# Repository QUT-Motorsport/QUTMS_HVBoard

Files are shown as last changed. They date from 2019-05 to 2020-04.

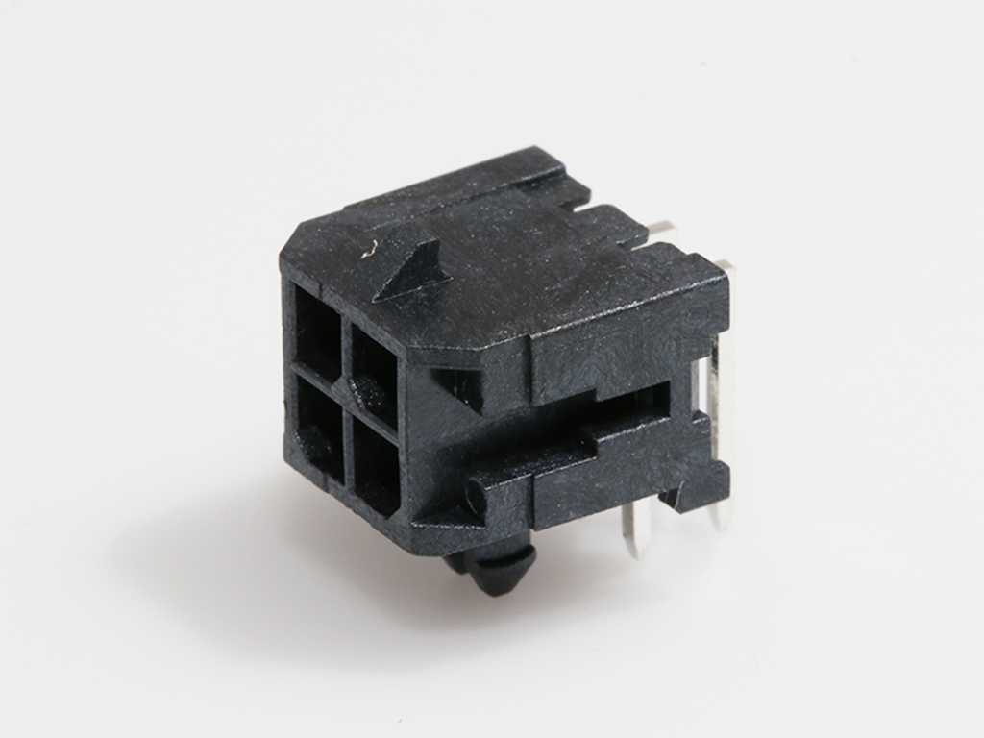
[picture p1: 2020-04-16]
hardware/QUTMS_HVBoard_V1_1/0430450400_hires.jpg

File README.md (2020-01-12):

QUTMS_Banner
# HV Board
The HV Board resides inside the HV box directly infront of the accumulator and monitors the tractive system in various ways.

## Features

- CANBUS Interface using the MCP2517 ic
- Isolated analog TSAL enable/disable signalling
- IMD state sensing and powering
- Tractive system current measurement
- UART debugging header

## Functions

Whilst the BSPD circitry is located on the shutdown board, the HV board powers the device and has an amplifier to boost the signal before it makes its way through the wiring harness.

In order to detect when the tractive system has a voltage more than 60V present, there is an isolated circuit on board that compares a divided TS voltage with a reference voltage. It also has a mosfet to drive the TS active and TS inactive signals to the TSAL board.

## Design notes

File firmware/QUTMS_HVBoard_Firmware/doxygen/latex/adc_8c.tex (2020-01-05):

\hypertarget{adc_8c}{}\doxysection{adc.\+c File Reference}
\label{adc_8c}\index{adc.c@{adc.c}}

Analogue to digital conversion.  

{\ttfamily \#include \char`\"{}adc.\+h\char`\"{}}\newline
{\ttfamily \#include $<$avr/interrupt.\+h$>$}\newline
{\ttfamily \#include $<$avr/io.\+h$>$}\newline
{\ttfamily \#include $<$avr/pgmspace.\+h$>$}\newline
{\ttfamily \#include $<$util/delay.\+h$>$}\newline
\doxysubsection*{Functions}
\begin{DoxyCompactItemize}
\item 
void \mbox{\hyperlink{adc_8c_a1e942fcd91f79d49e4ddb8d7e9d3ef95}{adc\+\_\+init}} ()
\item 
void \mbox{\hyperlink{adc_8c_af95038404db6216aa1860a35929b90ac}{adc\+\_\+set\+\_\+prescalar}} (uint8\+\_\+t prescalar)
\item 
uint16\+\_\+t \mbox{\hyperlink{adc_8c_a67d34c1378ba0871293df7b6a387de60}{adc\+\_\+read}} (uint8\+\_\+t adc\+\_\+channel)
\end{DoxyCompactItemize}

\doxysubsection{Detailed Description}
Analogue to digital conversion. 

\begin{DoxyAuthor}{Author}
Zoe Goodward 
\end{DoxyAuthor}

\doxysubsection{Function Documentation}
\mbox{\Hypertarget{adc_8c_a1e942fcd91f79d49e4ddb8d7e9d3ef95}\label{adc_8c_a1e942fcd91f79d49e4ddb8d7e9d3ef95}} 
\index{adc.c@{adc.c}!adc\_init@{adc\_init}}
\index{adc\_init@{adc\_init}!adc.c@{adc.c}}
\doxysubsubsection{\texorpdfstring{adc\_init()}{adc\_init()}}
{\footnotesize\ttfamily void adc\+\_\+init (\begin{DoxyParamCaption}{ }\end{DoxyParamCaption})}

Initializes the analogue to digital conversion by first selecting the voltage reference and then setting the A\+DC Enable bit, A\+D\+EN in A\+D\+C\+S\+RA. \begin{DoxyReturn}{Returns}
void 
\end{DoxyReturn}
\mbox{\Hypertarget{adc_8c_a67d34c1378ba0871293df7b6a387de60}\label{adc_8c_a67d34c1378ba0871293df7b6a387de60}} 
\index{adc.c@{adc.c}!adc\_read@{adc\_read}}
\index{adc\_read@{adc\_read}!adc.c@{adc.c}}
\doxysubsubsection{\texorpdfstring{adc\_read()}{adc\_read()}}
{\footnotesize\ttfamily uint16\+\_\+t adc\+\_\+read (\begin{DoxyParamCaption}\item[{uint8\+\_\+t}]{adc\+\_\+channel }\end{DoxyParamCaption})}

Reads an analogue input voltage and converts it to a 10-\/bit digital value through successive approximation. 
\begin{DoxyParams}{Parameters}
{\em adc\+\_\+channel} & Selected analogue input channel \\
\hline
\end{DoxyParams}
\begin{DoxyReturn}{Returns}
Pass the 10 bit A\+DC number to requesting function 
\end{DoxyReturn}
\mbox{\Hypertarget{adc_8c_af95038404db6216aa1860a35929b90ac}\label{adc_8c_af95038404db6216aa1860a35929b90ac}} 
\index{adc.c@{adc.c}!adc\_set\_prescalar@{adc\_set\_prescalar}}
\index{adc\_set\_prescalar@{adc\_set\_prescalar}!adc.c@{adc.c}}
\doxysubsubsection{\texorpdfstring{adc\_set\_prescalar()}{adc\_set\_prescalar()}}
{\footnotesize\ttfamily void adc\+\_\+set\+\_\+prescalar (\begin{DoxyParamCaption}\item[{uint8\+\_\+t}]{prescalar }\end{DoxyParamCaption})}

Sets the prescalar. \begin{DoxyReturn}{Returns}
void 
\end{DoxyReturn}

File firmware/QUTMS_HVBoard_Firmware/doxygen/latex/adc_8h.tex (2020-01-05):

\hypertarget{adc_8h}{}\doxysection{adc.\+h File Reference}
\label{adc_8h}\index{adc.h@{adc.h}}

Analogue to digital conversion.  

{\ttfamily \#include $<$avr/io.\+h$>$}\newline
{\ttfamily \#include $<$util/delay.\+h$>$}\newline
{\ttfamily \#include $<$avr/interrupt.\+h$>$}\newline
{\ttfamily \#include $<$avr/pgmspace.\+h$>$}\newline
\doxysubsection*{Macros}
\begin{DoxyCompactItemize}
\item 
\#define \mbox{\hyperlink{adc_8h_a97010ca07f7fab62f9fb4b4c404e6a90}{A\+D\+C\+\_\+\+P\+R\+E\+S\+C\+A\+L\+E\+\_\+\+M\+A\+SK}}~0b11111000
\end{DoxyCompactItemize}
\doxysubsection*{Functions}
\begin{DoxyCompactItemize}
\item 
void \mbox{\hyperlink{adc_8h_a1e942fcd91f79d49e4ddb8d7e9d3ef95}{adc\+\_\+init}} ()
\item 
uint16\+\_\+t \mbox{\hyperlink{adc_8h_a67d34c1378ba0871293df7b6a387de60}{adc\+\_\+read}} (uint8\+\_\+t adc\+\_\+channel)
\end{DoxyCompactItemize}

\doxysubsection{Detailed Description}
Analogue to digital conversion. 

\begin{DoxyAuthor}{Author}
Zoe Goodward 
\end{DoxyAuthor}

\doxysubsection{Macro Definition Documentation}
\mbox{\Hypertarget{adc_8h_a97010ca07f7fab62f9fb4b4c404e6a90}\label{adc_8h_a97010ca07f7fab62f9fb4b4c404e6a90}} 
\index{adc.h@{adc.h}!ADC\_PRESCALE\_MASK@{ADC\_PRESCALE\_MASK}}
\index{ADC\_PRESCALE\_MASK@{ADC\_PRESCALE\_MASK}!adc.h@{adc.h}}
\doxysubsubsection{\texorpdfstring{ADC\_PRESCALE\_MASK}{ADC\_PRESCALE\_MASK}}
{\footnotesize\ttfamily \#define A\+D\+C\+\_\+\+P\+R\+E\+S\+C\+A\+L\+E\+\_\+\+M\+A\+SK~0b11111000}

\doxysubsection{Function Documentation}
\mbox{\Hypertarget{adc_8h_a1e942fcd91f79d49e4ddb8d7e9d3ef95}\label{adc_8h_a1e942fcd91f79d49e4ddb8d7e9d3ef95}} 
\index{adc.h@{adc.h}!adc\_init@{adc\_init}}
\index{adc\_init@{adc\_init}!adc.h@{adc.h}}
\doxysubsubsection{\texorpdfstring{adc\_init()}{adc\_init()}}
{\footnotesize\ttfamily void adc\+\_\+init (\begin{DoxyParamCaption}{ }\end{DoxyParamCaption})}

Initializes the analogue to digital conversion by first selecting the voltage reference and then setting the A\+DC Enable bit, A\+D\+EN in A\+D\+C\+S\+RA. \begin{DoxyReturn}{Returns}
void 
\end{DoxyReturn}
\mbox{\Hypertarget{adc_8h_a67d34c1378ba0871293df7b6a387de60}\label{adc_8h_a67d34c1378ba0871293df7b6a387de60}} 
\index{adc.h@{adc.h}!adc\_read@{adc\_read}}
\index{adc\_read@{adc\_read}!adc.h@{adc.h}}
\doxysubsubsection{\texorpdfstring{adc\_read()}{adc\_read()}}
{\footnotesize\ttfamily uint16\+\_\+t adc\+\_\+read (\begin{DoxyParamCaption}\item[{uint8\+\_\+t}]{adc\+\_\+channel }\end{DoxyParamCaption})}

Reads an analogue input voltage and converts it to a 10-\/bit digital value through successive approximation. 
\begin{DoxyParams}{Parameters}
{\em adc\+\_\+channel} & Selected analogue input channel \\
\hline
\end{DoxyParams}
\begin{DoxyReturn}{Returns}
Pass the 10 bit A\+DC number to requesting function 
\end{DoxyReturn}

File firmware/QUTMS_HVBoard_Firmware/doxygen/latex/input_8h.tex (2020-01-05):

\hypertarget{input_8h}{}\doxysection{input.\+h File Reference}
\label{input_8h}\index{input.h@{input.h}}

This file defines the outputs and inputs of the pins of the M\+CU test.  

\doxysubsection*{Macros}
\begin{DoxyCompactItemize}
\item 
\#define \mbox{\hyperlink{input_8h_ad344f4bc1bb96945391f1edcd2060d60}{C\+A\+N\+\_\+\+C\+S\+\_\+\+P\+O\+RT}}~P\+O\+R\+TB
\item 
\#define \mbox{\hyperlink{input_8h_ab8cc8ec9bfd0e83fbc693b57f91545b1}{C\+A\+N\+\_\+\+CS}}~P\+I\+N\+B3
\item 
\#define \mbox{\hyperlink{input_8h_a5e4af61c9cda09a07019a625496aad51}{C\+A\+N\+\_\+\+I\+NT}}~P\+I\+N\+B0
\item 
\#define \mbox{\hyperlink{input_8h_ab7f73ee6874d571893c07b78293b9524}{L\+E\+D\+\_\+A}}~P\+I\+N\+D6
\item 
\#define \mbox{\hyperlink{input_8h_a2d0969469518b59d85bfa78504cffef9}{L\+E\+D\+\_\+B}}~P\+I\+N\+D7
\item 
\#define \mbox{\hyperlink{input_8h_a9fbaade4f52377099fe27dfde7cc6b34}{L\+E\+D\+\_\+\+A\+\_\+\+ON}}~P\+O\+R\+TD $\vert$= 0b01000000
\item 
\#define \mbox{\hyperlink{input_8h_ab351a7c43c4d7fe53191df69a0d0d4cb}{L\+E\+D\+\_\+\+A\+\_\+\+O\+FF}}~P\+O\+R\+TD \&= $\sim$0b01000000
\item 
\#define \mbox{\hyperlink{input_8h_a1429fd4e85c4d8e419b4a05aba730df5}{L\+E\+D\+\_\+\+B\+\_\+\+ON}}~P\+O\+R\+TD $\vert$= 0b10000000
\item 
\#define \mbox{\hyperlink{input_8h_a1552ab4bdb99c586585fc78c969848bc}{L\+E\+D\+\_\+\+B\+\_\+\+O\+FF}}~P\+O\+R\+TD \&= $\sim$0b10000000
\item 
\#define \mbox{\hyperlink{input_8h_af309cf9cb33c25c407e3b8679cf9d601}{L\+E\+D\+\_\+\+A\+\_\+\+T\+O\+G\+G\+LE}}~P\+O\+R\+TD $^\wedge$= 0b01000000
\item 
\#define \mbox{\hyperlink{input_8h_a0c1fba754d8d18f94fa73189b6fdcd78}{I\+M\+D\+\_\+\+R\+EG}}~P\+I\+NA
\item 
\#define \mbox{\hyperlink{input_8h_ac7e14c87447fabc3ab90eff695976def}{I\+M\+D\+\_\+\+S\+T\+A\+T\+US}}~P\+I\+N\+A2
\item 
\#define \mbox{\hyperlink{input_8h_a40c6fc36b705933b5671a86806cbdb3e}{H\+V\+\_\+\+S\+E\+N\+S\+E\+\_\+\+R\+EG}}~P\+I\+NA
\item 
\#define \mbox{\hyperlink{input_8h_a1ee6fbbcd4ac34f1c64c7e2d414127b1}{H\+V\+\_\+\+S\+E\+N\+S\+E\+\_\+\+S\+T\+A\+T\+US}}~P\+I\+N\+A0
\end{DoxyCompactItemize}

\doxysubsection{Detailed Description}
This file defines the outputs and inputs of the pins of the M\+CU test. 

\begin{DoxyAuthor}{Author}
Zoe Goodward 
\end{DoxyAuthor}

\doxysubsection{Macro Definition Documentation}
\mbox{\Hypertarget{input_8h_ab8cc8ec9bfd0e83fbc693b57f91545b1}\label{input_8h_ab8cc8ec9bfd0e83fbc693b57f91545b1}} 
\index{input.h@{input.h}!CAN\_CS@{CAN\_CS}}
\index{CAN\_CS@{CAN\_CS}!input.h@{input.h}}
\doxysubsubsection{\texorpdfstring{CAN\_CS}{CAN\_CS}}
{\footnotesize\ttfamily \#define C\+A\+N\+\_\+\+CS~P\+I\+N\+B3}

\mbox{\Hypertarget{input_8h_ad344f4bc1bb96945391f1edcd2060d60}\label{input_8h_ad344f4bc1bb96945391f1edcd2060d60}} 
\index{input.h@{input.h}!CAN\_CS\_PORT@{CAN\_CS\_PORT}}
\index{CAN\_CS\_PORT@{CAN\_CS\_PORT}!input.h@{input.h}}
\doxysubsubsection{\texorpdfstring{CAN\_CS\_PORT}{CAN\_CS\_PORT}}
{\footnotesize\ttfamily \#define C\+A\+N\+\_\+\+C\+S\+\_\+\+P\+O\+RT~P\+O\+R\+TB}

\mbox{\Hypertarget{input_8h_a5e4af61c9cda09a07019a625496aad51}\label{input_8h_a5e4af61c9cda09a07019a625496aad51}} 
\index{input.h@{input.h}!CAN\_INT@{CAN\_INT}}
\index{CAN\_INT@{CAN\_INT}!input.h@{input.h}}
\doxysubsubsection{\texorpdfstring{CAN\_INT}{CAN\_INT}}
{\footnotesize\ttfamily \#define C\+A\+N\+\_\+\+I\+NT~P\+I\+N\+B0}

\mbox{\Hypertarget{input_8h_a40c6fc36b705933b5671a86806cbdb3e}\label{input_8h_a40c6fc36b705933b5671a86806cbdb3e}} 
\index{input.h@{input.h}!HV\_SENSE\_REG@{HV\_SENSE\_REG}}
\index{HV\_SENSE\_REG@{HV\_SENSE\_REG}!input.h@{input.h}}
\doxysubsubsection{\texorpdfstring{HV\_SENSE\_REG}{HV\_SENSE\_REG}}
{\footnotesize\ttfamily \#define H\+V\+\_\+\+S\+E\+N\+S\+E\+\_\+\+R\+EG~P\+I\+NA}

\mbox{\Hypertarget{input_8h_a1ee6fbbcd4ac34f1c64c7e2d414127b1}\label{input_8h_a1ee6fbbcd4ac34f1c64c7e2d414127b1}} 
\index{input.h@{input.h}!HV\_SENSE\_STATUS@{HV\_SENSE\_STATUS}}
\index{HV\_SENSE\_STATUS@{HV\_SENSE\_STATUS}!input.h@{input.h}}
\doxysubsubsection{\texorpdfstring{HV\_SENSE\_STATUS}{HV\_SENSE\_STATUS}}
{\footnotesize\ttfamily \#define H\+V\+\_\+\+S\+E\+N\+S\+E\+\_\+\+S\+T\+A\+T\+US~P\+I\+N\+A0}

\mbox{\Hypertarget{input_8h_a0c1fba754d8d18f94fa73189b6fdcd78}\label{input_8h_a0c1fba754d8d18f94fa73189b6fdcd78}} 
\index{input.h@{input.h}!IMD\_REG@{IMD\_REG}}
\index{IMD\_REG@{IMD\_REG}!input.h@{input.h}}
\doxysubsubsection{\texorpdfstring{IMD\_REG}{IMD\_REG}}
{\footnotesize\ttfamily \#define I\+M\+D\+\_\+\+R\+EG~P\+I\+NA}

\mbox{\Hypertarget{input_8h_ac7e14c87447fabc3ab90eff695976def}\label{input_8h_ac7e14c87447fabc3ab90eff695976def}} 
\index{input.h@{input.h}!IMD\_STATUS@{IMD\_STATUS}}
\index{IMD\_STATUS@{IMD\_STATUS}!input.h@{input.h}}
\doxysubsubsection{\texorpdfstring{IMD\_STATUS}{IMD\_STATUS}}
{\footnotesize\ttfamily \#define I\+M\+D\+\_\+\+S\+T\+A\+T\+US~P\+I\+N\+A2}

\mbox{\Hypertarget{input_8h_ab7f73ee6874d571893c07b78293b9524}\label{input_8h_ab7f73ee6874d571893c07b78293b9524}} 
\index{input.h@{input.h}!LED\_A@{LED\_A}}
\index{LED\_A@{LED\_A}!input.h@{input.h}}
\doxysubsubsection{\texorpdfstring{LED\_A}{LED\_A}}
{\footnotesize\ttfamily \#define L\+E\+D\+\_\+A~P\+I\+N\+D6}

\mbox{\Hypertarget{input_8h_ab351a7c43c4d7fe53191df69a0d0d4cb}\label{input_8h_ab351a7c43c4d7fe53191df69a0d0d4cb}} 
\index{input.h@{input.h}!LED\_A\_OFF@{LED\_A\_OFF}}
\index{LED\_A\_OFF@{LED\_A\_OFF}!input.h@{input.h}}
\doxysubsubsection{\texorpdfstring{LED\_A\_OFF}{LED\_A\_OFF}}
{\footnotesize\ttfamily \#define L\+E\+D\+\_\+\+A\+\_\+\+O\+FF~P\+O\+R\+TD \&= $\sim$0b01000000}

\mbox{\Hypertarget{input_8h_a9fbaade4f52377099fe27dfde7cc6b34}\label{input_8h_a9fbaade4f52377099fe27dfde7cc6b34}} 
\index{input.h@{input.h}!LED\_A\_ON@{LED\_A\_ON}}
\index{LED\_A\_ON@{LED\_A\_ON}!input.h@{input.h}}
\doxysubsubsection{\texorpdfstring{LED\_A\_ON}{LED\_A\_ON}}
{\footnotesize\ttfamily \#define L\+E\+D\+\_\+\+A\+\_\+\+ON~P\+O\+R\+TD $\vert$= 0b01000000}

\mbox{\Hypertarget{input_8h_af309cf9cb33c25c407e3b8679cf9d601}\label{input_8h_af309cf9cb33c25c407e3b8679cf9d601}} 
\index{input.h@{input.h}!LED\_A\_TOGGLE@{LED\_A\_TOGGLE}}
\index{LED\_A\_TOGGLE@{LED\_A\_TOGGLE}!input.h@{input.h}}
\doxysubsubsection{\texorpdfstring{LED\_A\_TOGGLE}{LED\_A\_TOGGLE}}
{\footnotesize\ttfamily \#define L\+E\+D\+\_\+\+A\+\_\+\+T\+O\+G\+G\+LE~P\+O\+R\+TD $^\wedge$= 0b01000000}

\mbox{\Hypertarget{input_8h_a2d0969469518b59d85bfa78504cffef9}\label{input_8h_a2d0969469518b59d85bfa78504cffef9}} 
\index{input.h@{input.h}!LED\_B@{LED\_B}}
\index{LED\_B@{LED\_B}!input.h@{input.h}}
\doxysubsubsection{\texorpdfstring{LED\_B}{LED\_B}}
{\footnotesize\ttfamily \#define L\+E\+D\+\_\+B~P\+I\+N\+D7}

\mbox{\Hypertarget{input_8h_a1552ab4bdb99c586585fc78c969848bc}\label{input_8h_a1552ab4bdb99c586585fc78c969848bc}} 
\index{input.h@{input.h}!LED\_B\_OFF@{LED\_B\_OFF}}
\index{LED\_B\_OFF@{LED\_B\_OFF}!input.h@{input.h}}
\doxysubsubsection{\texorpdfstring{LED\_B\_OFF}{LED\_B\_OFF}}
{\footnotesize\ttfamily \#define L\+E\+D\+\_\+\+B\+\_\+\+O\+FF~P\+O\+R\+TD \&= $\sim$0b10000000}

\mbox{\Hypertarget{input_8h_a1429fd4e85c4d8e419b4a05aba730df5}\label{input_8h_a1429fd4e85c4d8e419b4a05aba730df5}} 
\index{input.h@{input.h}!LED\_B\_ON@{LED\_B\_ON}}
\index{LED\_B\_ON@{LED\_B\_ON}!input.h@{input.h}}
\doxysubsubsection{\texorpdfstring{LED\_B\_ON}{LED\_B\_ON}}
{\footnotesize\ttfamily \#define L\+E\+D\+\_\+\+B\+\_\+\+ON~P\+O\+R\+TD $\vert$= 0b10000000}

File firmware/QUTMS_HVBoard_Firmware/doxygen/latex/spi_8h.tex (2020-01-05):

\hypertarget{spi_8h}{}\doxysection{spi.\+h File Reference}
\label{spi_8h}\index{spi.h@{spi.h}}

This file declares the variables and functions that are used for S\+PI.  

\doxysubsection*{Macros}
\begin{DoxyCompactItemize}
\item 
\#define \mbox{\hyperlink{spi_8h_ab1dcc9464e3fcb94922386e8a7f53f21}{S\+P\+I\+\_\+\+M\+O\+DE}}~0
\item 
\#define \mbox{\hyperlink{spi_8h_add43c9bea4c3651888ddd858eee36c28}{S\+P\+I\+\_\+\+C\+L\+K\+\_\+\+R\+A\+TE}}~0
\item 
\#define \mbox{\hyperlink{spi_8h_a1039e667b18eb11df8ab4e168546200b}{S\+P\+I\+\_\+\+M\+S\+TR}}~1
\item 
\#define \mbox{\hyperlink{spi_8h_ae77748f6ed40c1bc713dbe98e29df4ea}{S\+P\+I\+\_\+\+M\+S\+B\+F\+I\+R\+ST}}~0
\item 
\#define \mbox{\hyperlink{spi_8h_afa9464d1e027eef964a5857fe8b90dca}{S\+P\+I\+\_\+\+I\+N\+T\+\_\+\+E\+N\+A\+B\+LE}}~0
\item 
\#define \mbox{\hyperlink{spi_8h_abcc154757b25dda166dce9045be9ab84}{S\+P\+I\+\_\+\+I\+N\+T\+E\+R\+R\+U\+PT}}~0
\item 
\#define \mbox{\hyperlink{spi_8h_a29348dd4519241c6ac23773790cdcbc0}{S\+P\+I\+\_\+\+D\+A\+T\+A\+\_\+\+O\+R\+D\+ER}}~0
\item 
\#define \mbox{\hyperlink{spi_8h_a1125dd08de06106973c5addde9a41687}{S\+P\+I\+\_\+\+M\+S\+T\+R\+\_\+\+M\+O\+DE}}~1
\item 
\#define \mbox{\hyperlink{spi_8h_a4cafe948918622f80c27db640c6c23c6}{S\+P\+I\+\_\+\+C\+L\+K\+\_\+\+P\+O\+L\+A\+R\+I\+TY}}~0
\item 
\#define \mbox{\hyperlink{spi_8h_a430ad9ccffd42f4427ba22fcc8167c64}{S\+P\+I\+\_\+\+C\+L\+K\+\_\+\+P\+H\+A\+SE}}~0
\item 
\#define \mbox{\hyperlink{spi_8h_a53afee17bd48bf3bed716e205d99c56c}{S\+P\+I\+\_\+\+C\+L\+K\+\_\+\+R\+A\+T\+E0}}~0
\item 
\#define \mbox{\hyperlink{spi_8h_a6a2fef08c9ee4445775d410da8321646}{S\+P\+I\+\_\+\+C\+L\+K\+\_\+\+R\+A\+T\+E1}}~0
\item 
\#define \mbox{\hyperlink{spi_8h_ad073a074d1b6f05b785db2558d922cc7}{D\+B\+L\+\_\+\+C\+LK}}~0
\end{DoxyCompactItemize}
\doxysubsection*{Functions}
\begin{DoxyCompactItemize}
\item 
void \mbox{\hyperlink{spi_8h_ae756a6229ad1607c3db6c5ce964ec0e4}{spi\+\_\+init}} (uint8\+\_\+t clk\+Rate0, uint8\+\_\+t clk\+Rate1)
\item 
uint8\+\_\+t \mbox{\hyperlink{spi_8h_a294e1c93357a516fb97c2e8c5a64af39}{spi\+\_\+send\+\_\+byte}} (uint8\+\_\+t data)
\item 
void \mbox{\hyperlink{spi_8h_a7fccfe54b22144461137578f104388db}{spi\+\_\+transfer\+\_\+buffer}} (uint8\+\_\+t $\ast$buf, uint8\+\_\+t count)
\item 
uint16\+\_\+t \mbox{\hyperlink{spi_8h_abad8f17f55a4258840e87d16704535d5}{spi\+\_\+transfer\+\_\+16}} (uint16\+\_\+t data)
\end{DoxyCompactItemize}

\doxysubsection{Detailed Description}
This file declares the variables and functions that are used for S\+PI. 

\begin{DoxyAuthor}{Author}
Zoe Goodward 
\end{DoxyAuthor}

\doxysubsection{Macro Definition Documentation}
\mbox{\Hypertarget{spi_8h_ad073a074d1b6f05b785db2558d922cc7}\label{spi_8h_ad073a074d1b6f05b785db2558d922cc7}} 
\index{spi.h@{spi.h}!DBL\_CLK@{DBL\_CLK}}
\index{DBL\_CLK@{DBL\_CLK}!spi.h@{spi.h}}
\doxysubsubsection{\texorpdfstring{DBL\_CLK}{DBL\_CLK}}
{\footnotesize\ttfamily \#define D\+B\+L\+\_\+\+C\+LK~0}

\mbox{\Hypertarget{spi_8h_a430ad9ccffd42f4427ba22fcc8167c64}\label{spi_8h_a430ad9ccffd42f4427ba22fcc8167c64}} 
\index{spi.h@{spi.h}!SPI\_CLK\_PHASE@{SPI\_CLK\_PHASE}}
\index{SPI\_CLK\_PHASE@{SPI\_CLK\_PHASE}!spi.h@{spi.h}}
\doxysubsubsection{\texorpdfstring{SPI\_CLK\_PHASE}{SPI\_CLK\_PHASE}}
{\footnotesize\ttfamily \#define S\+P\+I\+\_\+\+C\+L\+K\+\_\+\+P\+H\+A\+SE~0}

\mbox{\Hypertarget{spi_8h_a4cafe948918622f80c27db640c6c23c6}\label{spi_8h_a4cafe948918622f80c27db640c6c23c6}} 
\index{spi.h@{spi.h}!SPI\_CLK\_POLARITY@{SPI\_CLK\_POLARITY}}
\index{SPI\_CLK\_POLARITY@{SPI\_CLK\_POLARITY}!spi.h@{spi.h}}
\doxysubsubsection{\texorpdfstring{SPI\_CLK\_POLARITY}{SPI\_CLK\_POLARITY}}
{\footnotesize\ttfamily \#define S\+P\+I\+\_\+\+C\+L\+K\+\_\+\+P\+O\+L\+A\+R\+I\+TY~0}

\mbox{\Hypertarget{spi_8h_add43c9bea4c3651888ddd858eee36c28}\label{spi_8h_add43c9bea4c3651888ddd858eee36c28}} 
\index{spi.h@{spi.h}!SPI\_CLK\_RATE@{SPI\_CLK\_RATE}}
\index{SPI\_CLK\_RATE@{SPI\_CLK\_RATE}!spi.h@{spi.h}}
\doxysubsubsection{\texorpdfstring{SPI\_CLK\_RATE}{SPI\_CLK\_RATE}}
{\footnotesize\ttfamily \#define S\+P\+I\+\_\+\+C\+L\+K\+\_\+\+R\+A\+TE~0}

\mbox{\Hypertarget{spi_8h_a53afee17bd48bf3bed716e205d99c56c}\label{spi_8h_a53afee17bd48bf3bed716e205d99c56c}} 
\index{spi.h@{spi.h}!SPI\_CLK\_RATE0@{SPI\_CLK\_RATE0}}
\index{SPI\_CLK\_RATE0@{SPI\_CLK\_RATE0}!spi.h@{spi.h}}
\doxysubsubsection{\texorpdfstring{SPI\_CLK\_RATE0}{SPI\_CLK\_RATE0}}
{\footnotesize\ttfamily \#define S\+P\+I\+\_\+\+C\+L\+K\+\_\+\+R\+A\+T\+E0~0}

\mbox{\Hypertarget{spi_8h_a6a2fef08c9ee4445775d410da8321646}\label{spi_8h_a6a2fef08c9ee4445775d410da8321646}} 
\index{spi.h@{spi.h}!SPI\_CLK\_RATE1@{SPI\_CLK\_RATE1}}
\index{SPI\_CLK\_RATE1@{SPI\_CLK\_RATE1}!spi.h@{spi.h}}
\doxysubsubsection{\texorpdfstring{SPI\_CLK\_RATE1}{SPI\_CLK\_RATE1}}
{\footnotesize\ttfamily \#define S\+P\+I\+\_\+\+C\+L\+K\+\_\+\+R\+A\+T\+E1~0}

\mbox{\Hypertarget{spi_8h_a29348dd4519241c6ac23773790cdcbc0}\label{spi_8h_a29348dd4519241c6ac23773790cdcbc0}} 
\index{spi.h@{spi.h}!SPI\_DATA\_ORDER@{SPI\_DATA\_ORDER}}
\index{SPI\_DATA\_ORDER@{SPI\_DATA\_ORDER}!spi.h@{spi.h}}
\doxysubsubsection{\texorpdfstring{SPI\_DATA\_ORDER}{SPI\_DATA\_ORDER}}
{\footnotesize\ttfamily \#define S\+P\+I\+\_\+\+D\+A\+T\+A\+\_\+\+O\+R\+D\+ER~0}

\mbox{\Hypertarget{spi_8h_afa9464d1e027eef964a5857fe8b90dca}\label{spi_8h_afa9464d1e027eef964a5857fe8b90dca}} 
\index{spi.h@{spi.h}!SPI\_INT\_ENABLE@{SPI\_INT\_ENABLE}}
\index{SPI\_INT\_ENABLE@{SPI\_INT\_ENABLE}!spi.h@{spi.h}}
\doxysubsubsection{\texorpdfstring{SPI\_INT\_ENABLE}{SPI\_INT\_ENABLE}}
{\footnotesize\ttfamily \#define S\+P\+I\+\_\+\+I\+N\+T\+\_\+\+E\+N\+A\+B\+LE~0}

\mbox{\Hypertarget{spi_8h_abcc154757b25dda166dce9045be9ab84}\label{spi_8h_abcc154757b25dda166dce9045be9ab84}} 
\index{spi.h@{spi.h}!SPI\_INTERRUPT@{SPI\_INTERRUPT}}
\index{SPI\_INTERRUPT@{SPI\_INTERRUPT}!spi.h@{spi.h}}
\doxysubsubsection{\texorpdfstring{SPI\_INTERRUPT}{SPI\_INTERRUPT}}
{\footnotesize\ttfamily \#define S\+P\+I\+\_\+\+I\+N\+T\+E\+R\+R\+U\+PT~0}

\mbox{\Hypertarget{spi_8h_ab1dcc9464e3fcb94922386e8a7f53f21}\label{spi_8h_ab1dcc9464e3fcb94922386e8a7f53f21}} 
\index{spi.h@{spi.h}!SPI\_MODE@{SPI\_MODE}}
\index{SPI\_MODE@{SPI\_MODE}!spi.h@{spi.h}}
\doxysubsubsection{\texorpdfstring{SPI\_MODE}{SPI\_MODE}}
{\footnotesize\ttfamily \#define S\+P\+I\+\_\+\+M\+O\+DE~0}

\mbox{\Hypertarget{spi_8h_ae77748f6ed40c1bc713dbe98e29df4ea}\label{spi_8h_ae77748f6ed40c1bc713dbe98e29df4ea}} 
\index{spi.h@{spi.h}!SPI\_MSBFIRST@{SPI\_MSBFIRST}}
\index{SPI\_MSBFIRST@{SPI\_MSBFIRST}!spi.h@{spi.h}}
\doxysubsubsection{\texorpdfstring{SPI\_MSBFIRST}{SPI\_MSBFIRST}}
{\footnotesize\ttfamily \#define S\+P\+I\+\_\+\+M\+S\+B\+F\+I\+R\+ST~0}

\mbox{\Hypertarget{spi_8h_a1039e667b18eb11df8ab4e168546200b}\label{spi_8h_a1039e667b18eb11df8ab4e168546200b}} 
\index{spi.h@{spi.h}!SPI\_MSTR@{SPI\_MSTR}}
\index{SPI\_MSTR@{SPI\_MSTR}!spi.h@{spi.h}}
\doxysubsubsection{\texorpdfstring{SPI\_MSTR}{SPI\_MSTR}}
{\footnotesize\ttfamily \#define S\+P\+I\+\_\+\+M\+S\+TR~1}

\mbox{\Hypertarget{spi_8h_a1125dd08de06106973c5addde9a41687}\label{spi_8h_a1125dd08de06106973c5addde9a41687}} 
\index{spi.h@{spi.h}!SPI\_MSTR\_MODE@{SPI\_MSTR\_MODE}}
\index{SPI\_MSTR\_MODE@{SPI\_MSTR\_MODE}!spi.h@{spi.h}}
\doxysubsubsection{\texorpdfstring{SPI\_MSTR\_MODE}{SPI\_MSTR\_MODE}}
{\footnotesize\ttfamily \#define S\+P\+I\+\_\+\+M\+S\+T\+R\+\_\+\+M\+O\+DE~1}

\doxysubsection{Function Documentation}
\mbox{\Hypertarget{spi_8h_ae756a6229ad1607c3db6c5ce964ec0e4}\label{spi_8h_ae756a6229ad1607c3db6c5ce964ec0e4}} 
\index{spi.h@{spi.h}!spi\_init@{spi\_init}}
\index{spi\_init@{spi\_init}!spi.h@{spi.h}}
\doxysubsubsection{\texorpdfstring{spi\_init()}{spi\_init()}}
{\footnotesize\ttfamily void spi\+\_\+init (\begin{DoxyParamCaption}\item[{uint8\+\_\+t}]{clk\+Rate0,  }\item[{uint8\+\_\+t}]{clk\+Rate1 }\end{DoxyParamCaption})}

\mbox{\Hypertarget{spi_8h_a294e1c93357a516fb97c2e8c5a64af39}\label{spi_8h_a294e1c93357a516fb97c2e8c5a64af39}} 
\index{spi.h@{spi.h}!spi\_send\_byte@{spi\_send\_byte}}
\index{spi\_send\_byte@{spi\_send\_byte}!spi.h@{spi.h}}
\doxysubsubsection{\texorpdfstring{spi\_send\_byte()}{spi\_send\_byte()}}
{\footnotesize\ttfamily uint8\+\_\+t spi\+\_\+send\+\_\+byte (\begin{DoxyParamCaption}\item[{uint8\+\_\+t}]{data }\end{DoxyParamCaption})}

\mbox{\Hypertarget{spi_8h_abad8f17f55a4258840e87d16704535d5}\label{spi_8h_abad8f17f55a4258840e87d16704535d5}} 
\index{spi.h@{spi.h}!spi\_transfer\_16@{spi\_transfer\_16}}
\index{spi\_transfer\_16@{spi\_transfer\_16}!spi.h@{spi.h}}
\doxysubsubsection{\texorpdfstring{spi\_transfer\_16()}{spi\_transfer\_16()}}
{\footnotesize\ttfamily uint16\+\_\+t spi\+\_\+transfer\+\_\+16 (\begin{DoxyParamCaption}\item[{uint16\+\_\+t}]{data }\end{DoxyParamCaption})}

\mbox{\Hypertarget{spi_8h_a7fccfe54b22144461137578f104388db}\label{spi_8h_a7fccfe54b22144461137578f104388db}} 
\index{spi.h@{spi.h}!spi\_transfer\_buffer@{spi\_transfer\_buffer}}
\index{spi\_transfer\_buffer@{spi\_transfer\_buffer}!spi.h@{spi.h}}
\doxysubsubsection{\texorpdfstring{spi\_transfer\_buffer()}{spi\_transfer\_buffer()}}
{\footnotesize\ttfamily void spi\+\_\+transfer\+\_\+buffer (\begin{DoxyParamCaption}\item[{uint8\+\_\+t $\ast$}]{buf,  }\item[{uint8\+\_\+t}]{count }\end{DoxyParamCaption})}

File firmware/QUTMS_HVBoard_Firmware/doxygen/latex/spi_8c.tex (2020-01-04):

\hypertarget{spi_8c}{}\doxysection{spi.\+c File Reference}
\label{spi_8c}\index{spi.c@{spi.c}}

This file...  

{\ttfamily \#include $<$inttypes.\+h$>$}\newline
{\ttfamily \#include $<$stddef.\+h$>$}\newline
{\ttfamily \#include $<$avr/io.\+h$>$}\newline
{\ttfamily \#include \char`\"{}spi.\+h\char`\"{}}\newline
{\ttfamily \#include \char`\"{}input.\+h\char`\"{}}\newline
{\ttfamily \#include \char`\"{}U\+A\+R\+T.\+h\char`\"{}}\newline
\doxysubsection*{Functions}
\begin{DoxyCompactItemize}
\item 
void \mbox{\hyperlink{spi_8c_ae756a6229ad1607c3db6c5ce964ec0e4}{spi\+\_\+init}} (uint8\+\_\+t clk\+Rate0, uint8\+\_\+t clk\+Rate1)
\item 
uint8\+\_\+t \mbox{\hyperlink{spi_8c_a294e1c93357a516fb97c2e8c5a64af39}{spi\+\_\+send\+\_\+byte}} (uint8\+\_\+t data)
\item 
void \mbox{\hyperlink{spi_8c_a7fccfe54b22144461137578f104388db}{spi\+\_\+transfer\+\_\+buffer}} (uint8\+\_\+t $\ast$buf, uint8\+\_\+t count)
\item 
void \mbox{\hyperlink{spi_8c_aa8d2d6d1632faf9abbe03c3ed90d54d4}{spi\+\_\+disable}} (void)
\end{DoxyCompactItemize}

\doxysubsection{Detailed Description}
This file... 

\begin{DoxyAuthor}{Author}
Zoe Goodward 
\end{DoxyAuthor}
\begin{DoxyVersion}{Version}
V1.\+0.\+0 
\end{DoxyVersion}
\begin{DoxyDate}{Date}
2/08/2019 1\+:25\+:34 PM 
\end{DoxyDate}

\doxysubsection{Function Documentation}
\mbox{\Hypertarget{spi_8c_aa8d2d6d1632faf9abbe03c3ed90d54d4}\label{spi_8c_aa8d2d6d1632faf9abbe03c3ed90d54d4}} 
\index{spi.c@{spi.c}!spi\_disable@{spi\_disable}}
\index{spi\_disable@{spi\_disable}!spi.c@{spi.c}}
\doxysubsubsection{\texorpdfstring{spi\_disable()}{spi\_disable()}}
{\footnotesize\ttfamily void spi\+\_\+disable (\begin{DoxyParamCaption}\item[{void}]{ }\end{DoxyParamCaption})}

\mbox{\Hypertarget{spi_8c_ae756a6229ad1607c3db6c5ce964ec0e4}\label{spi_8c_ae756a6229ad1607c3db6c5ce964ec0e4}} 
\index{spi.c@{spi.c}!spi\_init@{spi\_init}}
\index{spi\_init@{spi\_init}!spi.c@{spi.c}}
\doxysubsubsection{\texorpdfstring{spi\_init()}{spi\_init()}}
{\footnotesize\ttfamily void spi\+\_\+init (\begin{DoxyParamCaption}\item[{uint8\+\_\+t}]{clk\+Rate0,  }\item[{uint8\+\_\+t}]{clk\+Rate1 }\end{DoxyParamCaption})}

\mbox{\Hypertarget{spi_8c_a294e1c93357a516fb97c2e8c5a64af39}\label{spi_8c_a294e1c93357a516fb97c2e8c5a64af39}} 
\index{spi.c@{spi.c}!spi\_send\_byte@{spi\_send\_byte}}
\index{spi\_send\_byte@{spi\_send\_byte}!spi.c@{spi.c}}
\doxysubsubsection{\texorpdfstring{spi\_send\_byte()}{spi\_send\_byte()}}
{\footnotesize\ttfamily uint8\+\_\+t spi\+\_\+send\+\_\+byte (\begin{DoxyParamCaption}\item[{uint8\+\_\+t}]{data }\end{DoxyParamCaption})}

\mbox{\Hypertarget{spi_8c_a7fccfe54b22144461137578f104388db}\label{spi_8c_a7fccfe54b22144461137578f104388db}} 
\index{spi.c@{spi.c}!spi\_transfer\_buffer@{spi\_transfer\_buffer}}
\index{spi\_transfer\_buffer@{spi\_transfer\_buffer}!spi.c@{spi.c}}
\doxysubsubsection{\texorpdfstring{spi\_transfer\_buffer()}{spi\_transfer\_buffer()}}
{\footnotesize\ttfamily void spi\+\_\+transfer\+\_\+buffer (\begin{DoxyParamCaption}\item[{uint8\+\_\+t $\ast$}]{buf,  }\item[{uint8\+\_\+t}]{count }\end{DoxyParamCaption})}

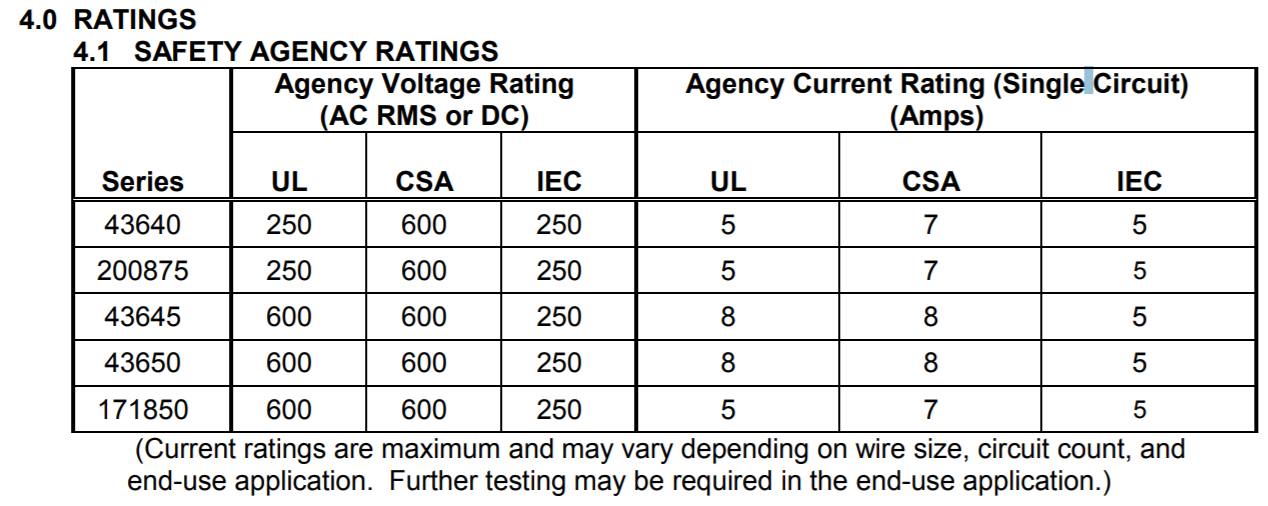
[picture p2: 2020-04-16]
hardware/QUTMS_HVBoard_V1_1/MicrofitHVRating.PNG

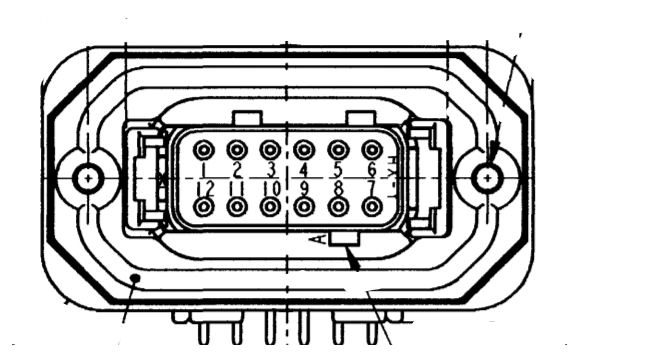
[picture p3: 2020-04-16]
hardware/QUTMS_HVBoard_V1_1/DTM12PCBRightFront.PNG

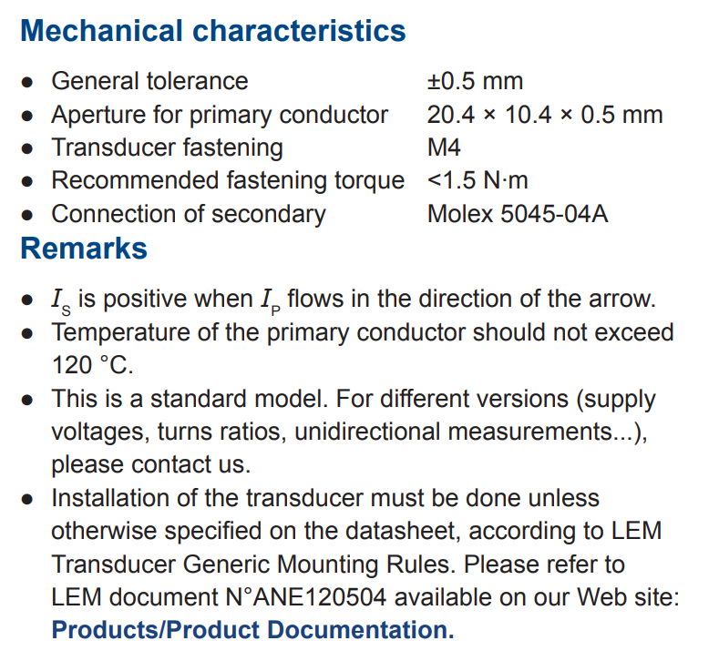
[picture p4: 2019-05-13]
hardware/QUTMS_HVBoard_V1_1/LEMSensorHASSCharactistics.PNG

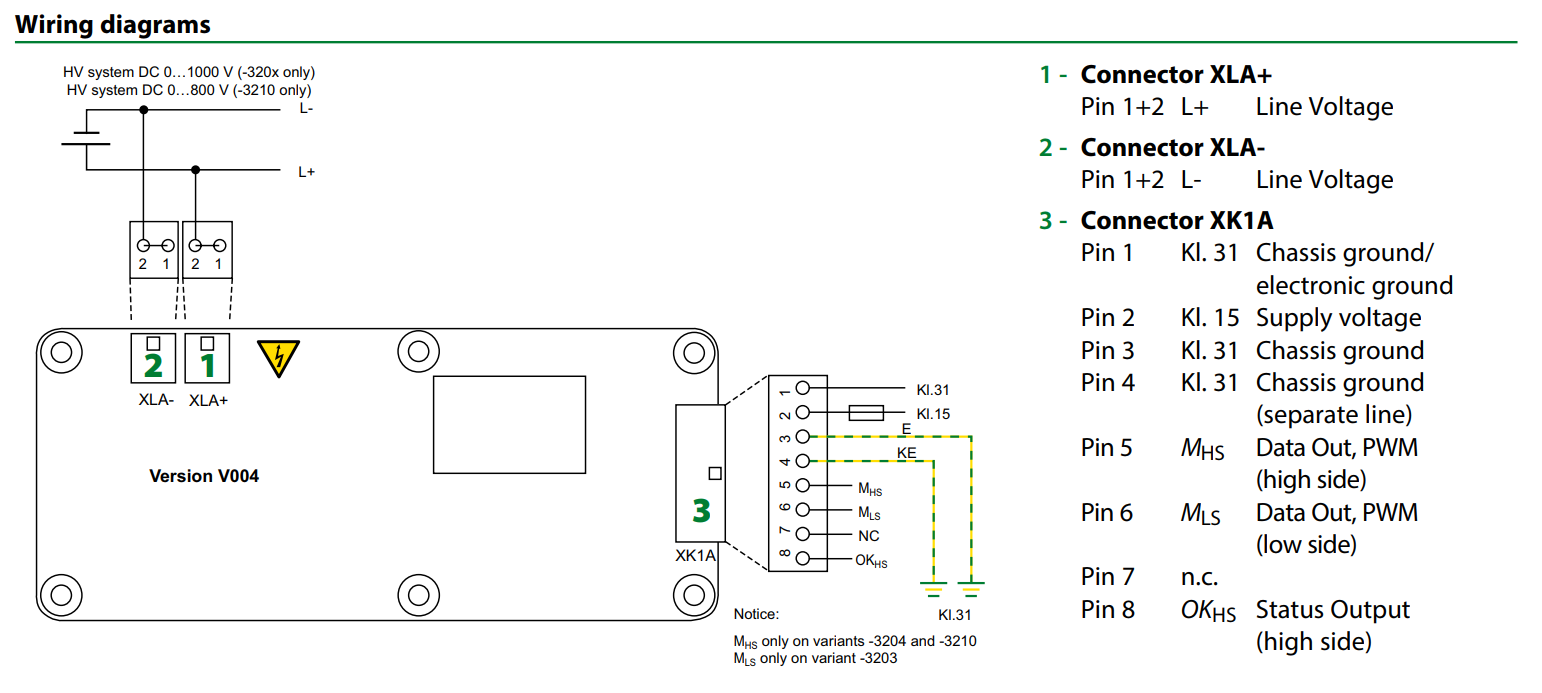
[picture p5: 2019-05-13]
hardware/QUTMS_HVBoard_V1_1/BenderIMDPinout.PNG

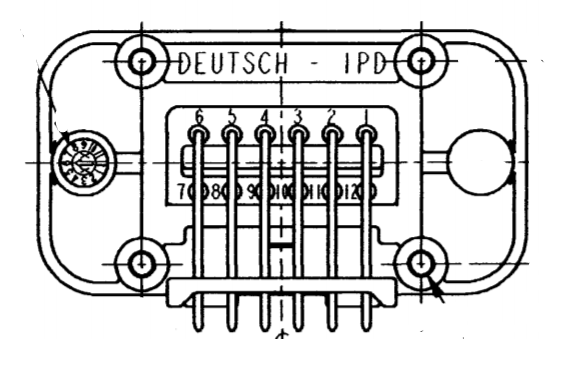
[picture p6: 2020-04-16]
hardware/QUTMS_HVBoard_V1_1/DTM12PCBRightBack.PNG

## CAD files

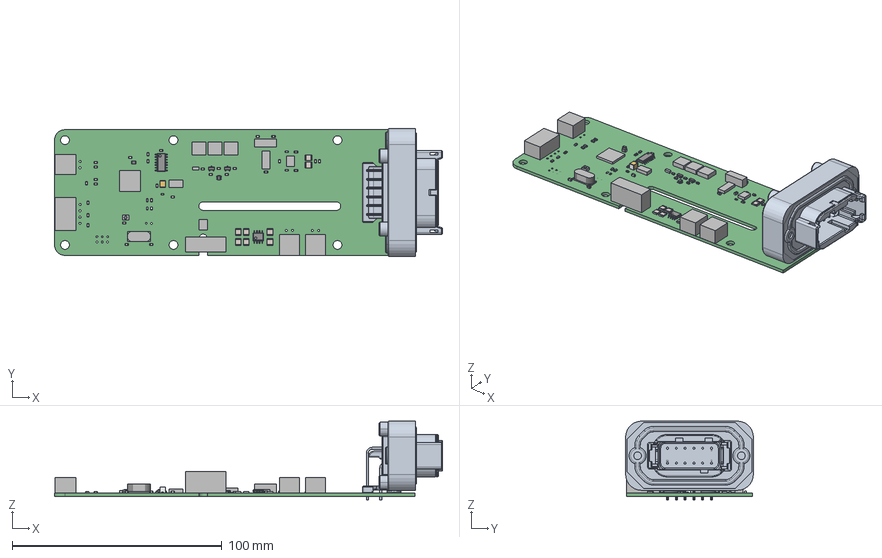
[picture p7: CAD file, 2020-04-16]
hardware/QUTMS_HVBoard_V1_1/Board.step
185.1 x 61.0 x 37.6 mm
Extruded x 152
BODY_M14A_20
LEAD_M14A_46 x 14
Open_CASCADE_STEP_translator_6.8_509.1.1
Open_CASCADE_STEP_translator_6.8_509.1.2
Open_CASCADE_STEP_translator_6.8_509.2.1
BODY_M08A_35
LEAD_M08A_57 x 8
MANIFOLD_SOLID_BREP_2784
MANIFOLD_SOLID_BREP_2935
MANIFOLD_SOLID_BREP_3086
MANIFOLD_SOLID_BREP_3237
Open_CASCADE_STEP_translator_6.8_9.1.1
Leader x 12
Open_CASCADE_STEP_translator_6.8_1.1.1 x 3
Open_CASCADE_STEP_translator_6.8_1.1.2
Open_CASCADE_STEP_translator_6.8_1.2.1
c-dtm13-12pa-99-3d

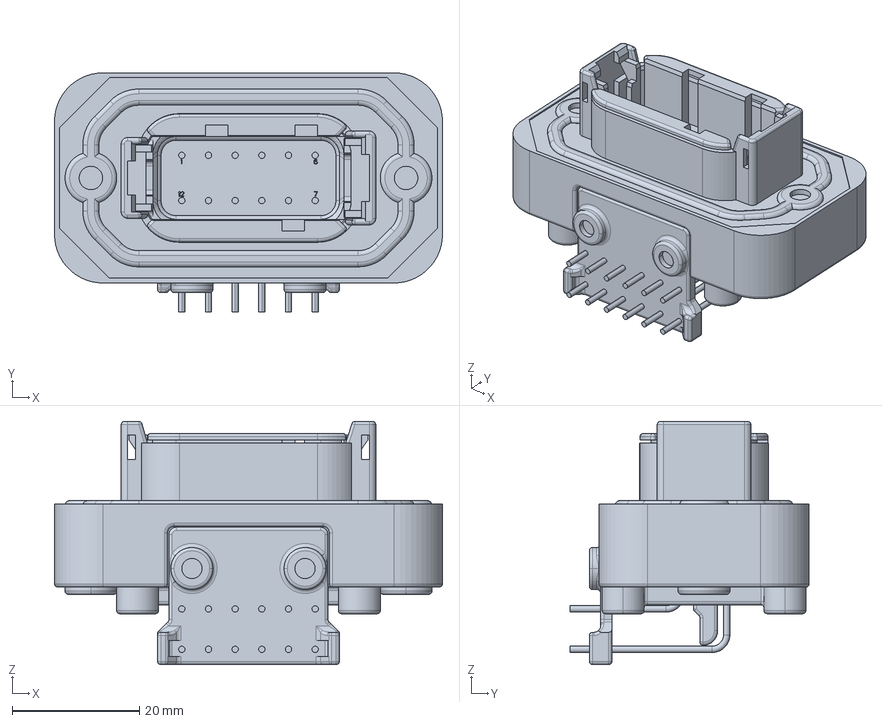
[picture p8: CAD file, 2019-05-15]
hardware/QUTMS_HVBoard_V1_1/c-dtm13-12pa-99-3d.stp
61.0 x 37.6 x 38.2 mm

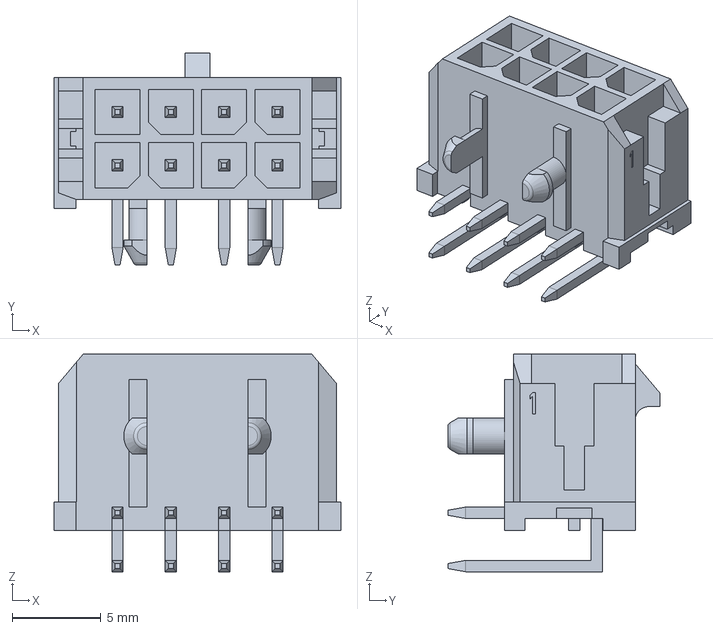
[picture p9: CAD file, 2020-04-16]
hardware/QUTMS_HVBoard_V1_1/430450800.stp
16.1 x 11.9 x 12.2 mm

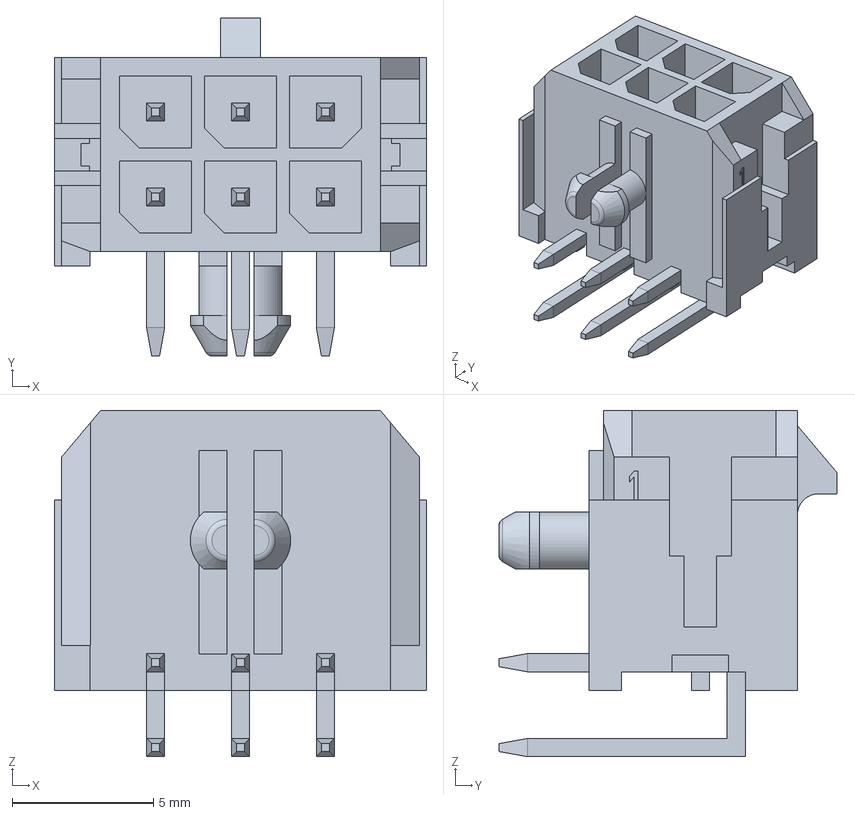
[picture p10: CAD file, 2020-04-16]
hardware/QUTMS_HVBoard_V1_1/430450600.stp
13.2 x 11.9 x 12.2 mm

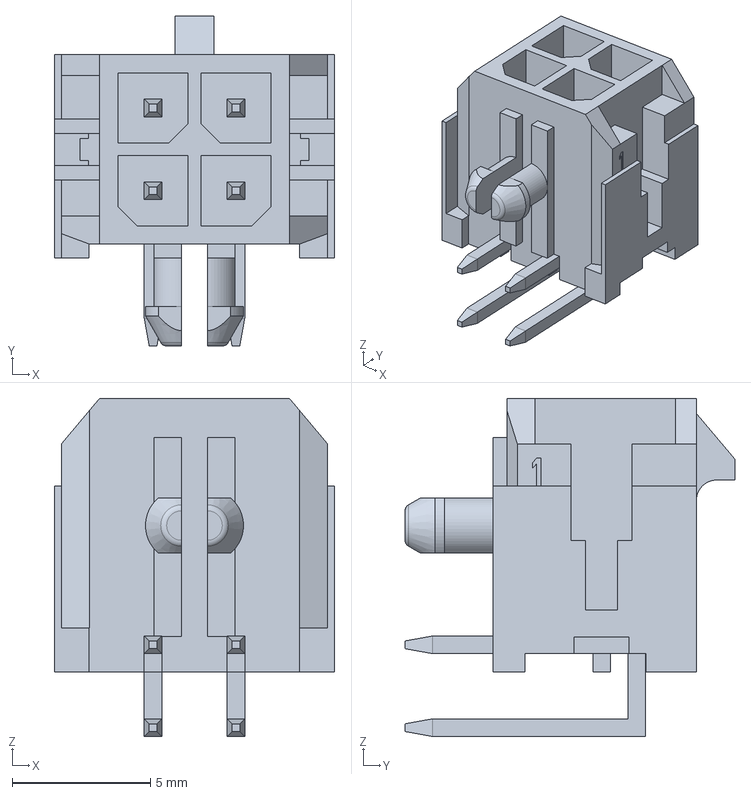
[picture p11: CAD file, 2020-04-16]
hardware/QUTMS_HVBoard_V1_1/430450400.stp
10.2 x 11.9 x 12.2 mm

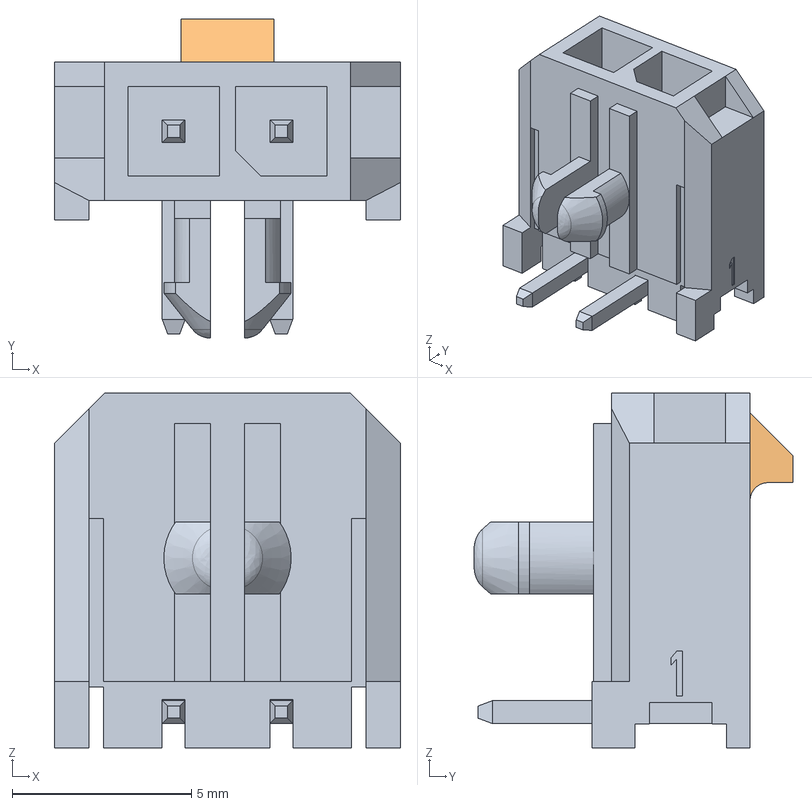
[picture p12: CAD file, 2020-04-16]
hardware/QUTMS_HVBoard_V1_1/436500201.stp
9.65 x 8.91 x 9.90 mm

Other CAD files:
hardware/QUTMS_HVBoard_V1/Board.DWG
hardware/QUTMS_HVBoard_V1_1/Board.DWG

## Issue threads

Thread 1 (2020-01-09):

Change programming header to right angle

liamkinne, 2020-01-09:
Currently if the IMD board is mounted on top of the HV board, the programming header is inaccessible. Changing the header to a right angle one pointing towards the edge of the board would fix this.

liamkinne, 2020-01-15:
resolved by #10

Closed 2020-01-15.

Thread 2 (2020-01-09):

Fix IMD mounting hole alignment

liamkinne, 2020-01-09:
The two middle holes to mount the IMD board to the HV board don't align. Fix this using the hole pattern defined in the IMD datasheet and check this by measuring the IMD.

mitchelljqegan, 2020-01-31:
Fixed in #11

Closed 2020-02-01.

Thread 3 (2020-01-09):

Replace digital isolator with an opto-isolator that has the correct isolation gap.

liamkinne, 2020-01-09:
This board almost didn't pass scrutineering at the competition because the digital isolator while being rated to the correct isolation, doesn't have a large enough gap between the legs of the GLV and HV side. An opto-isolator is what most teams use in this scenario.

mitchelljqegan, 2020-01-31:
Fixed in #11

Closed 2020-02-01.

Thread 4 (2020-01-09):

Move reset button to be accessible when the IMD is mounted above.

liamkinne, 2020-01-09:
Currently it is awkward to push the reset button when the IMD is mounted. Moving this to the edge of the board is nice to improve the usability.

liamkinne, 2020-01-15:
resolved by #10

Closed 2020-01-15.

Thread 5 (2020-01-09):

Change digital isolator to opto-isolator

liamkinne, 2020-01-09:
The digital isolator used to isolate the TSAL sensing circuit does not meet the minimum isolation gap of the rules. The easiest way to fix this is to change it to an opto-isolator.

This really needs to be tested because the opto-isolator works slightly differently.

mitchelljqegan, 2020-01-31:
Fixed in #11

Closed 2020-02-01.

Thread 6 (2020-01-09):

Add a ground pin to the UART header

liamkinne, 2020-01-09:
Having a ground reference on the uart header just makes it easier to connect the debugger.

liamkinne, 2020-01-15:
resolved by #10

Closed 2020-01-15.

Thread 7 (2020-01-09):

Move CANBUS TX and RX leds to the edge of the board

liamkinne, 2020-01-09:
Makes it easier to see them when the IMD board is mounted.

liamkinne, 2020-01-15:
resolved by #10

Closed 2020-01-15.

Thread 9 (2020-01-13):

Connect HV and isolated supply grounds.

liamkinne, 2020-01-13:
Since they both feed into the comparator, they need the same ground. This is done on the board with a bodge.

liamkinne, 2020-02-01:
not required anymore yay.

Closed 2020-02-01.

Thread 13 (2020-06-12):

HV - Serial output format

cwljohnson, 2020-06-12:
After #12 and maybe after https://github.com/QUT-Motorsport/QUTMS_CANSIM/issues/3:

This board has serial output connections on it. We want to be able to dump current information about the board over serial (eg CAN messages, program memory etc).

To do this, we need a set format for the output, so we can integrate into the config app.

cwljohnson, 2020-08-04:
no hv board

Closed 2020-08-04.

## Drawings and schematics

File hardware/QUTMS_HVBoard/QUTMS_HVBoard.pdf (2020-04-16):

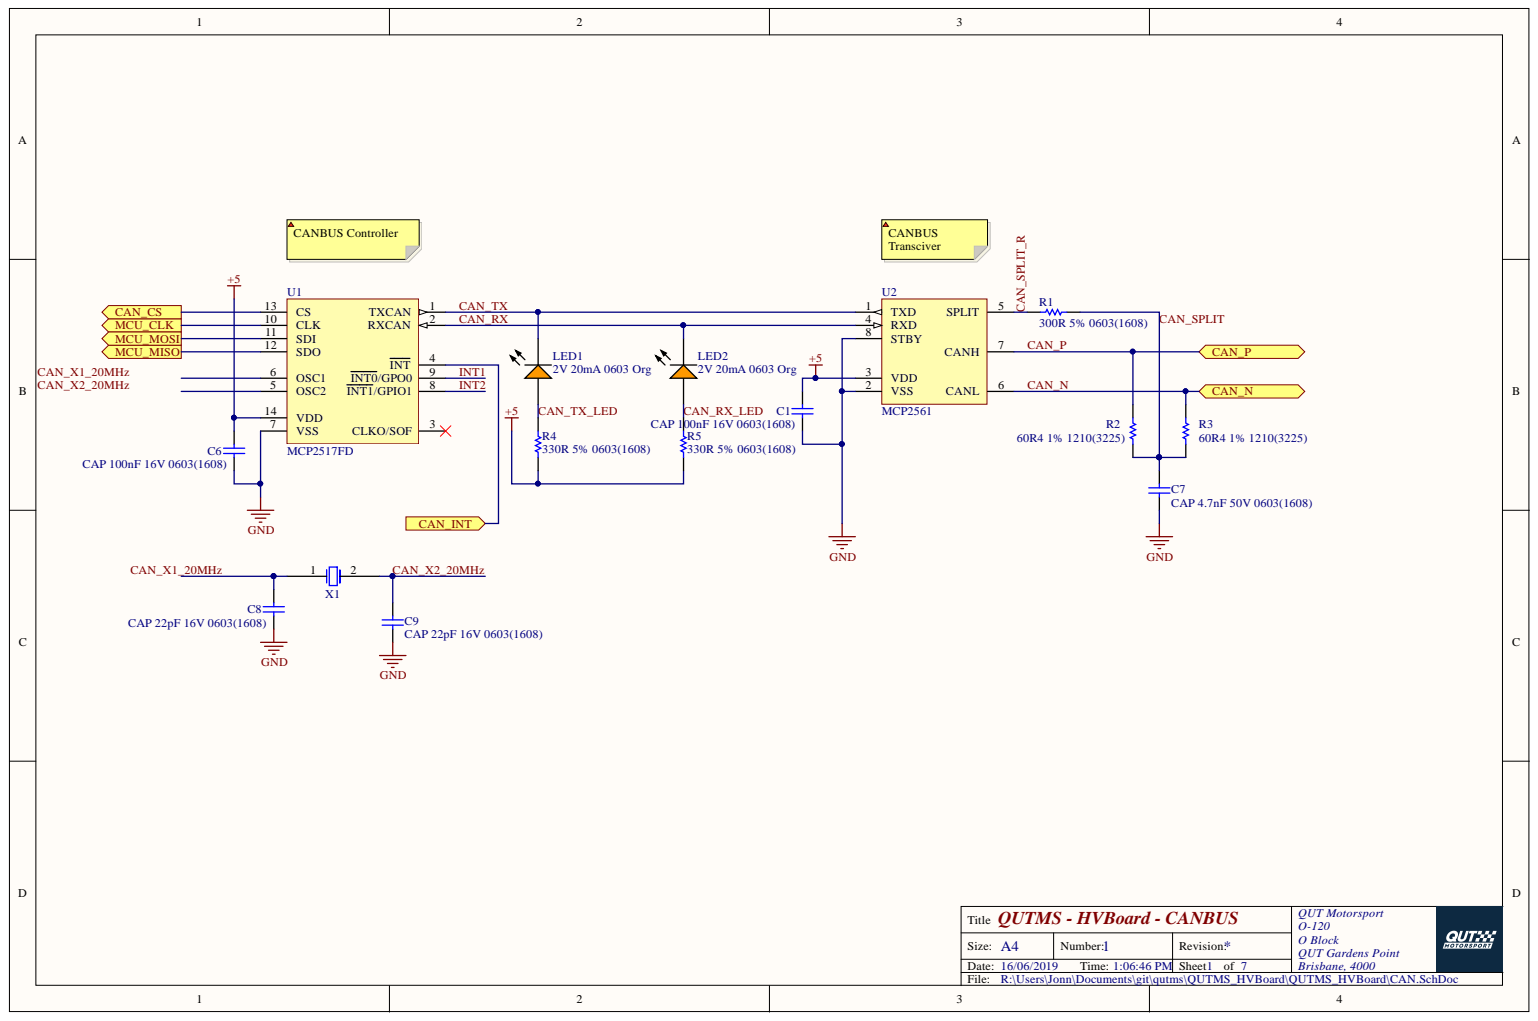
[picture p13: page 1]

2 | CA N _RX | 4

Q UTMS - HVBo ard - CANBUS T i t l e | Q UT Mo t o r sp o r t O-1 2 0 O B l ock Q UT G a rden s P o i n t B r i s b a ne, 4

A4 Size: | 1 N umber: | * Rev i s i o n :
Date: / / T ime: : : 6 PM | | Sheet o f

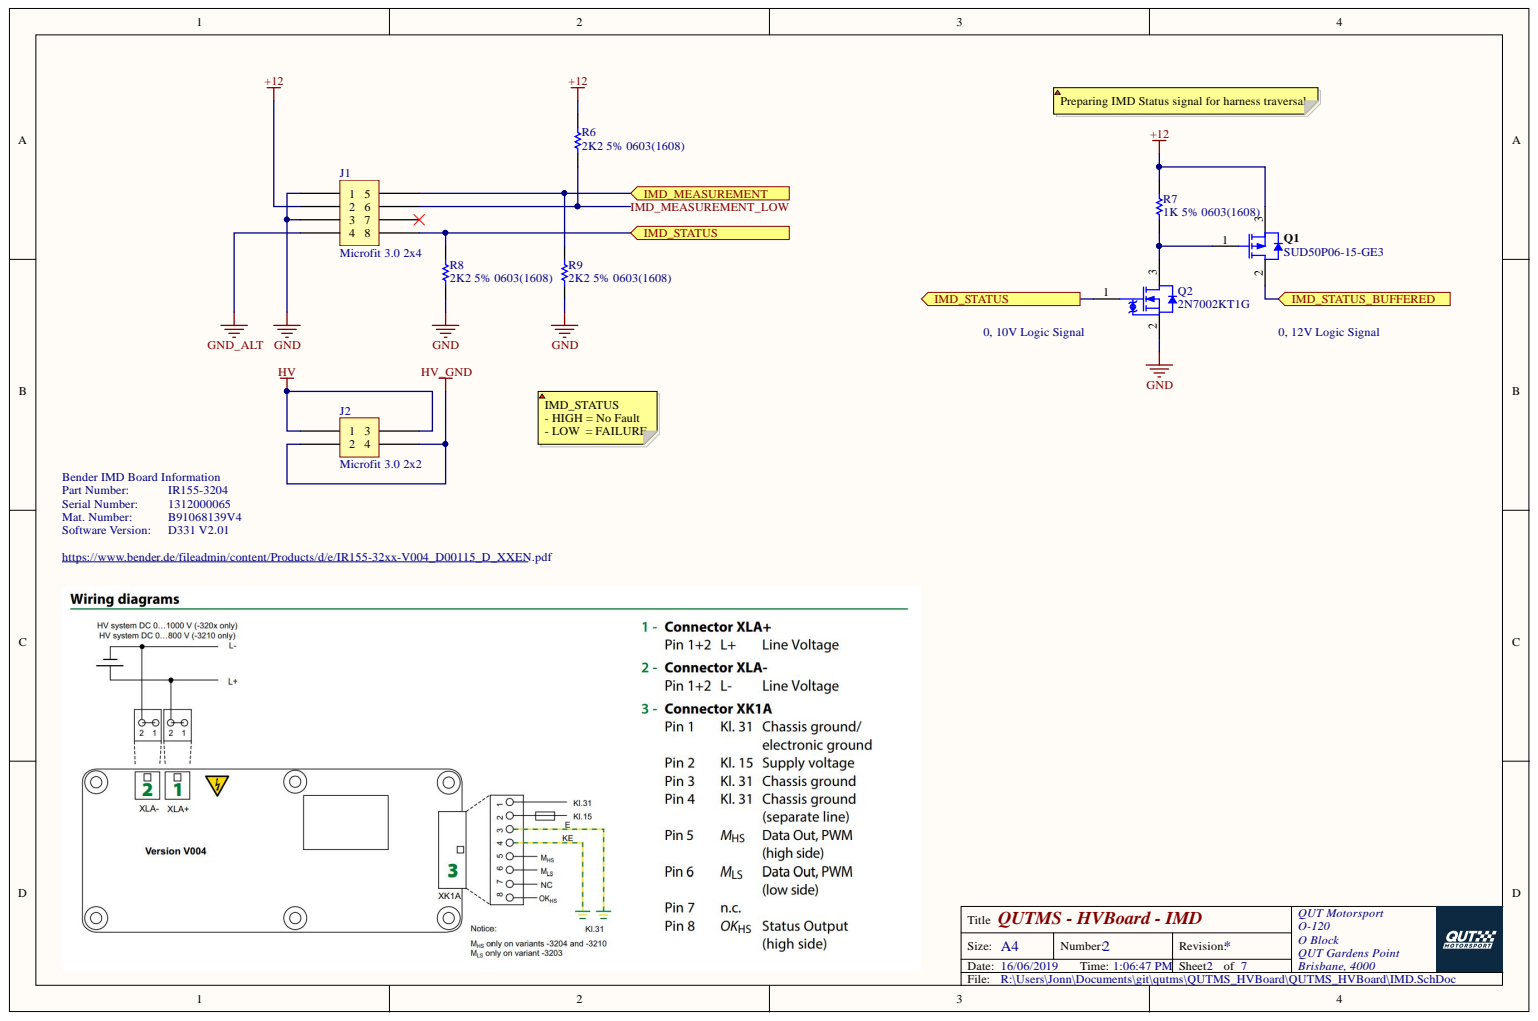
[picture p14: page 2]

Preparing IMD Status signal for harness traversal

Bender IMD Board Information
Part Number:
Serial Number:
Mat. Number:
Software Version:

https://www.bender.de/fileadmin/content/Products/d/e/IR155-32xx-V004_D00115_D_XXEN.pdf

QUTMS - HVBoard - IMD Title | QUT Motorsport O-120 O Block QUT Gardens Point Brisbane, 4000

A4 Size: | 2 Number: | * Revision:

16/06/2019 Time: 1:06:47 PM | | Sheet of 7

R:\Users\Jonn\Documents\git\qutms\QUTMS_HVBoard\QUTMS_HVBoard\IMD.SchDoc

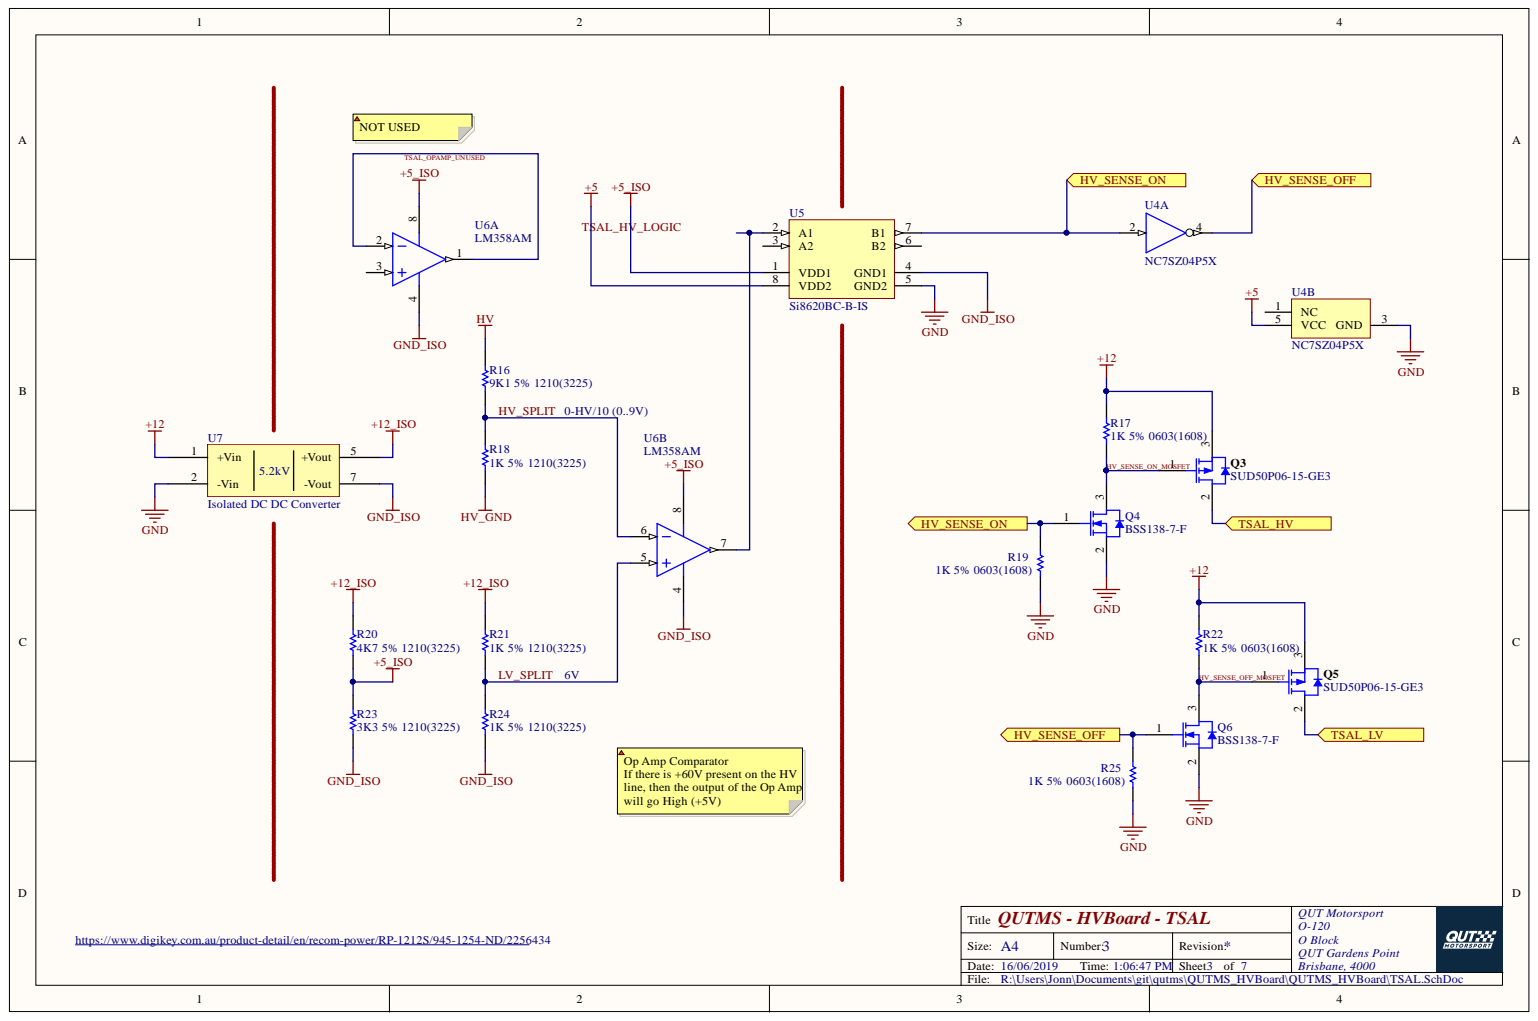
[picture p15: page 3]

VDD2 8

Isolated DC DC Converter

Op Amp Comparator
If there is +60V present on the HV
line, then the output of the Op Amp
will go High (+5V)

QUTMS - HVBoard - TSAL Title | QUT Motorsport O-120 O Block QUT Gardens Point Brisbane, 4000

https://www.digikey.com.au/product-detail/en/recom-power/RP-1212S/945-1254-ND/2256434

A4 Size: | 3 Number: | * Revision:

16/06/2019 Time: 1:06:47 PM | | Sheet of 7

R:\Users\Jonn\Documents\git\qutms\QUTMS_HVBoard\QUTMS_HVBoard\TSAL.SchDoc

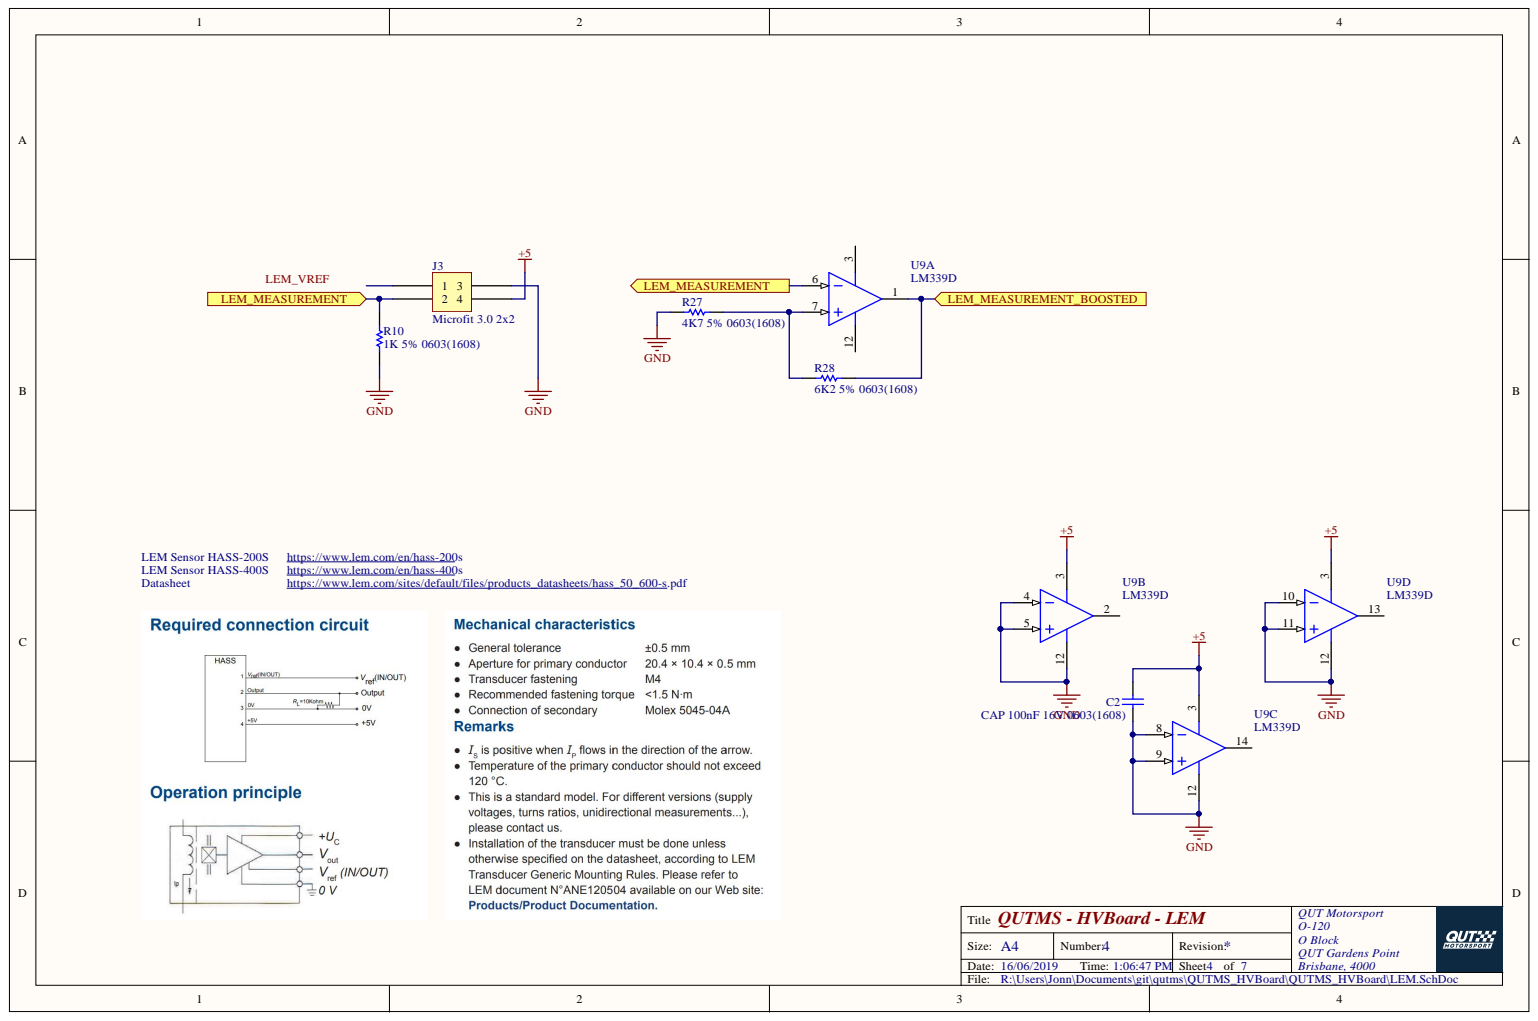
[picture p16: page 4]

https://www.lem.com/en/hass-200s
https://www.lem.com/en/hass-400s
https://www.lem.com/sites/default/files/products_datasheets/hass_50_600-s.pdf

QUTMS - HVBoard - LEM Title | QUT Motorsport O-120 O Block QUT Gardens Point Brisbane, 4000

A4 Size: | 4 Number: | * Revision:

16/06/2019 Time: 1:06:47 PM | | Sheet of 7

R:\Users\Jonn\Documents\git\qutms\QUTMS_HVBoard\QUTMS_HVBoard\LEM.SchDoc

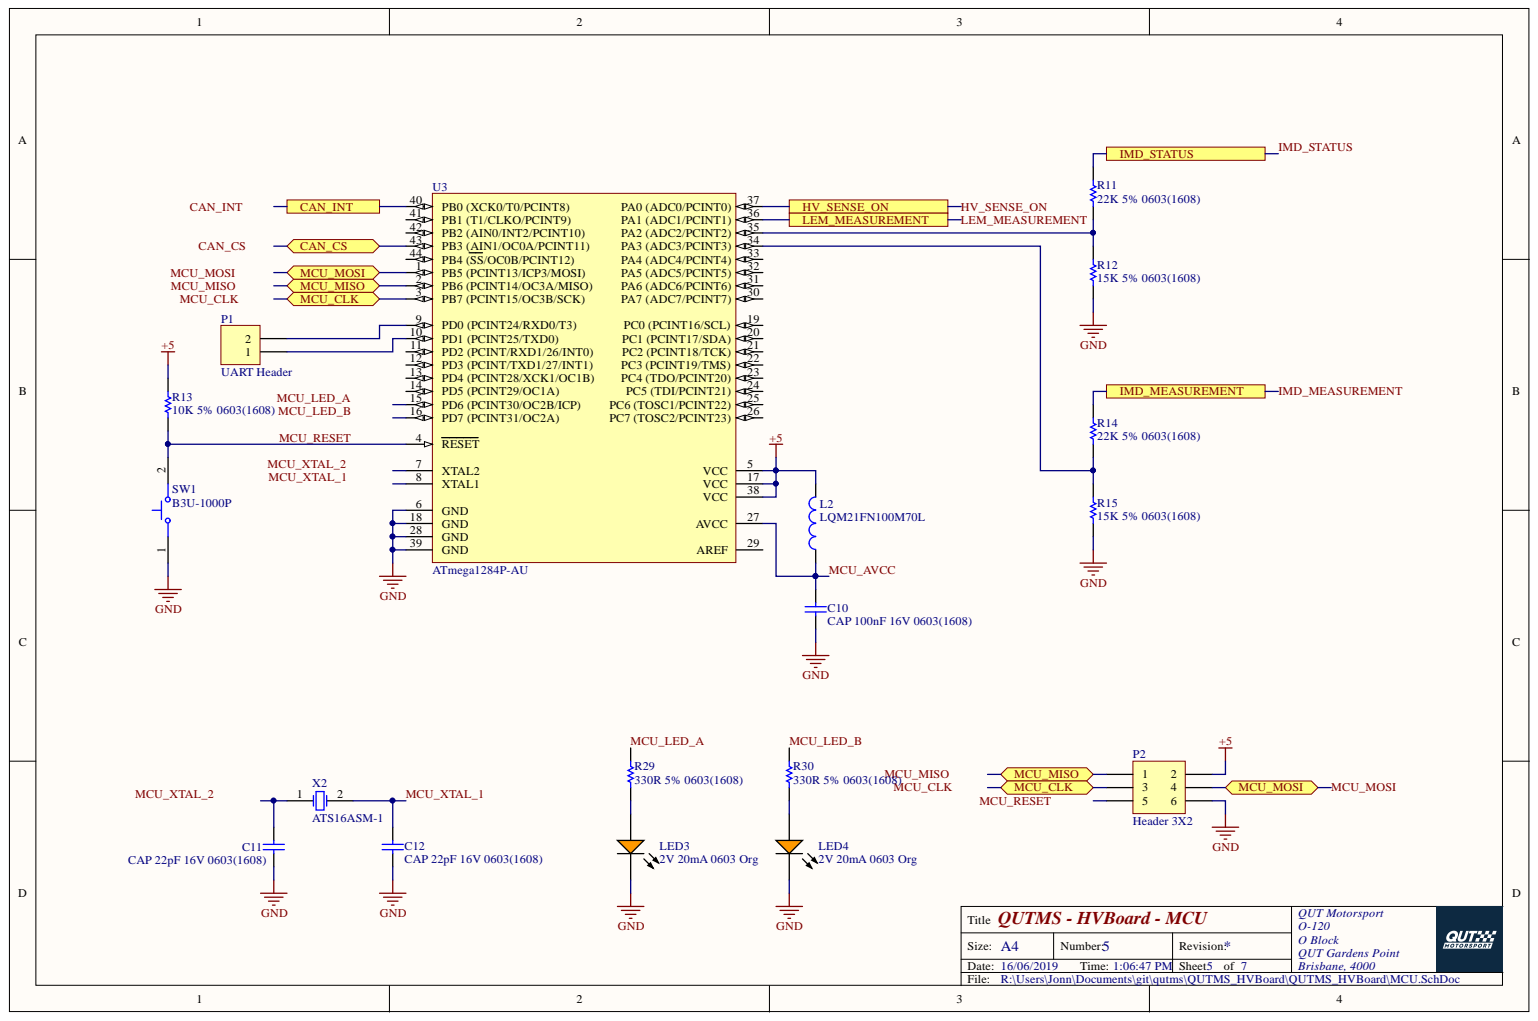
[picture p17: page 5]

GND 18

GND 39

QUTMS - HVBoard - MCU Title | QUT Motorsport O-120 O Block QUT Gardens Point Brisbane, 4000

A4 Size: | 5 Number: | * Revision:

16/06/2019 Time: 1:06:47 PM | | Sheet of 7

R:\Users\Jonn\Documents\git\qutms\QUTMS_HVBoard\QUTMS_HVBoard\MCU.SchDoc

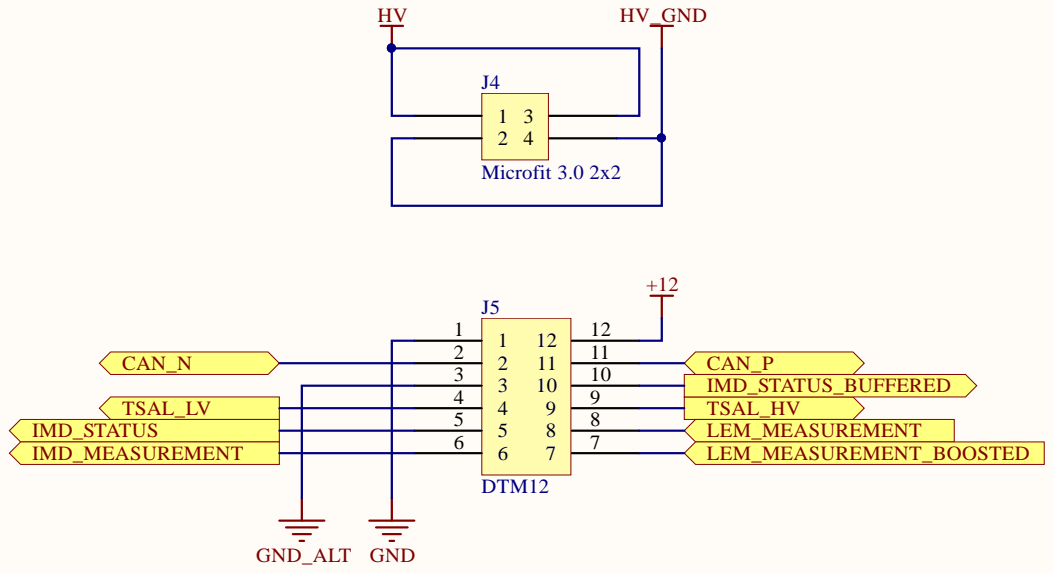
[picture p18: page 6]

QUTMS - HVBoard - Offboard Title | QUT Motorsport O-120 O Block QUT Gardens Point Brisbane, 4000

A4 Size: | 6 Number: | * Revision:

16/06/2019 Time: 1:06:48 PM | | Sheet of 7

R:\Users\Jonn\Documents\git\qutms\QUTMS_HVBoard\QUTMS_HVBoard\Offboard.SchDoc

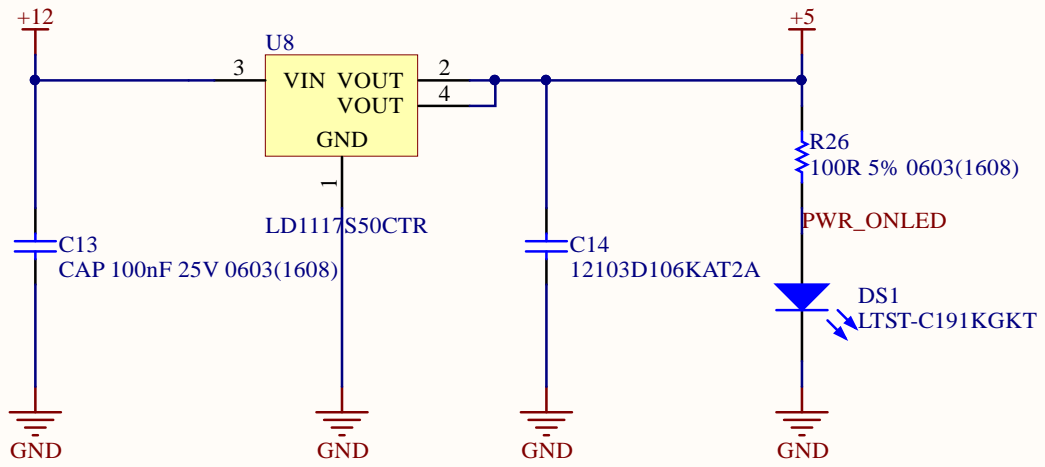
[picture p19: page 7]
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

A4 Size: | 7 N umber: | * Rev i s i o n :

/ / T ime: : : 8 PM | | Sheet o f

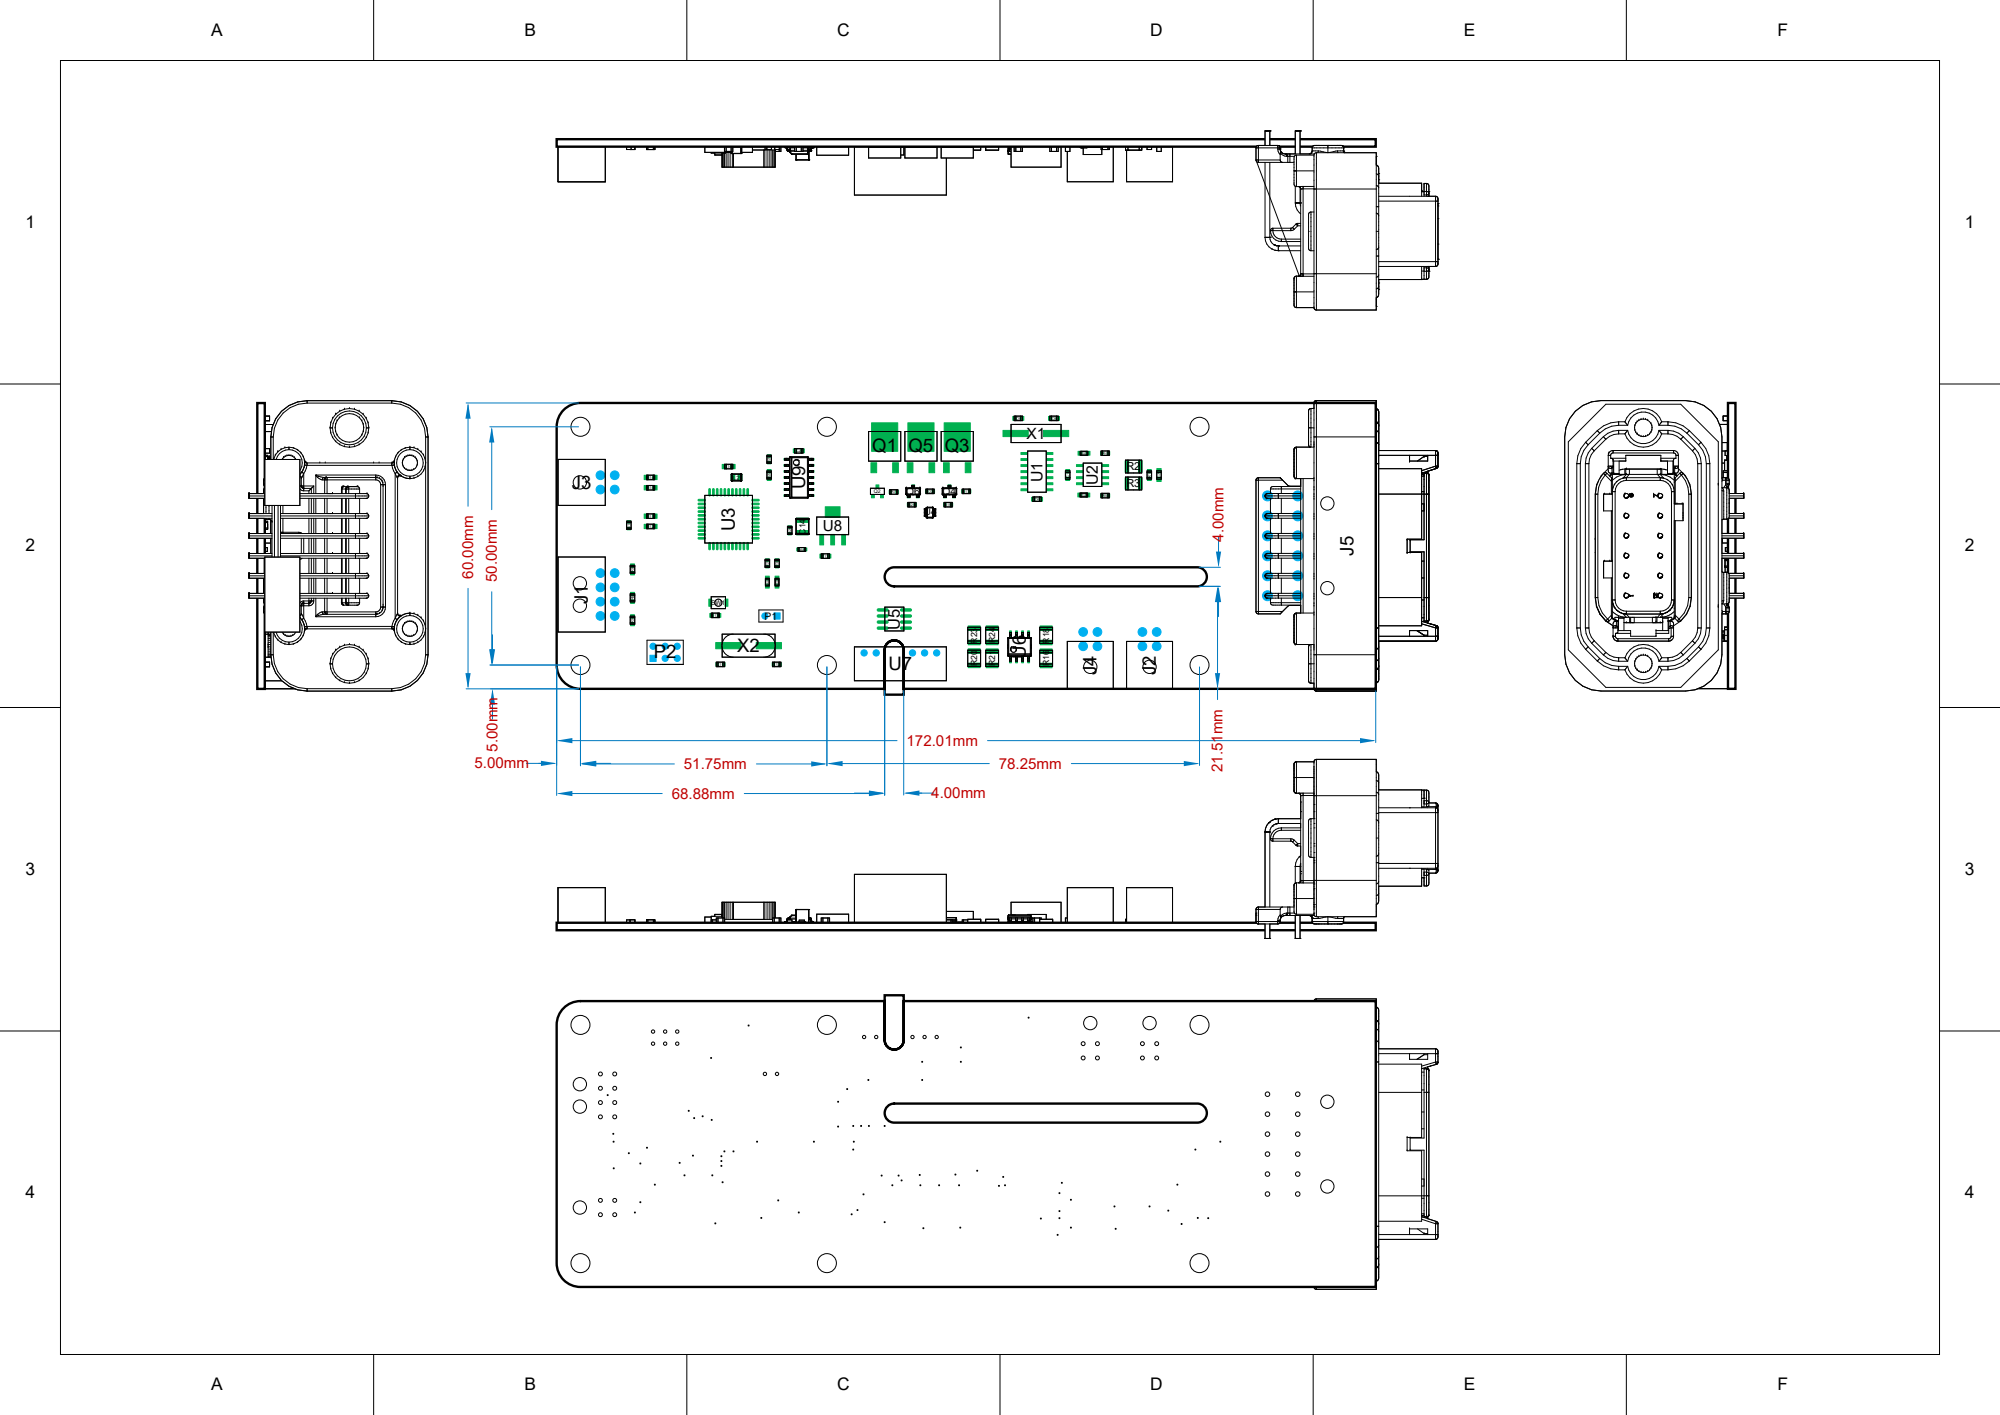
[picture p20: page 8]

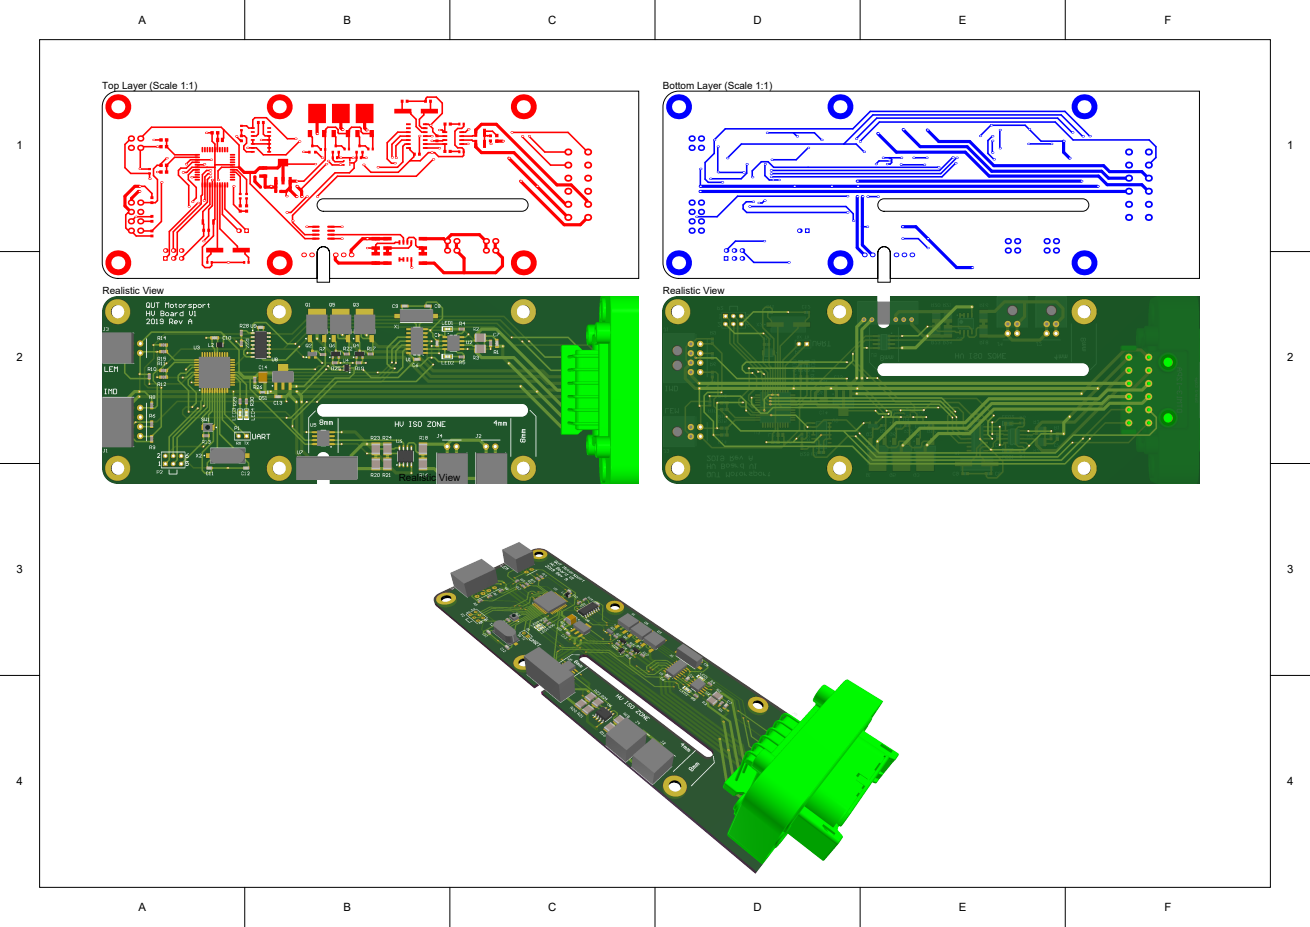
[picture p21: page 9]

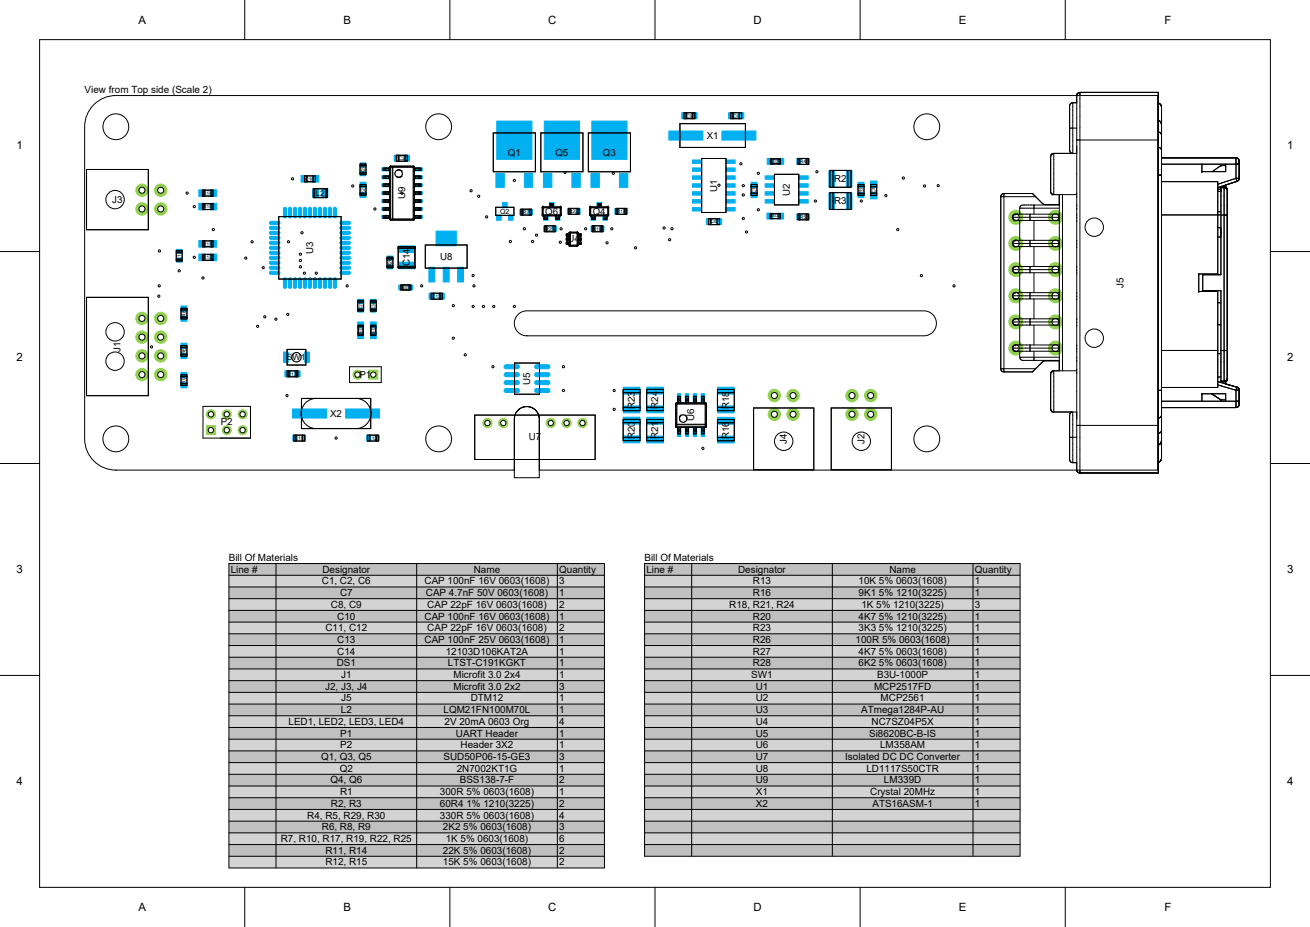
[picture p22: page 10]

View from Top side (Scale 2)

Line # | Designator | Name | Quantity

C1, C2, C6 | CAP 100nF 16V 0603(1608) | 3
C7 | CAP 4.7nF 50V 0603(1608) | 1
C8, C9 | CAP 22pF 16V 0603(1608) | 2
C10 | CAP 100nF 16V 0603(1608) | 1
C11, C12 | CAP 22pF 16V 0603(1608) | 2
C13 | CAP 100nF 25V 0603(1608) | 1
C14 | 12103D106KAT2A | 1
DS1 | LTST-C191KGKT | 1
J1 | Microfit 3.0 2x4 | 1
J2, J3, J4 | Microfit 3.0 2x2 | 3
J5 | DTM12 | 1
L2 | LQM21FN100M70L | 1

LED1, LED2, LED3, LED4 | 2V 20mA 0603 Org | 4

P1 | UART Header | 1
P2 | Header 3X2 | 1
Q1, Q3, Q5 | SUD50P06-15-GE3 | 3
Q2 | 2N7002KT1G | 1
Q4, Q6 | BSS138-7-F | 2
R1 | 300R 5% 0603(1608) | 1
R2, R3 | 60R4 1% 1210(3225) | 2
R4, R5, R29, R30 | 330R 5% 0603(1608) | 4
R6, R8, R9 | 2K2 5% 0603(1608) | 3

R11, R14 | 22K 5% 0603(1608)
R12, R15 | 15K 5% 0603(1608)

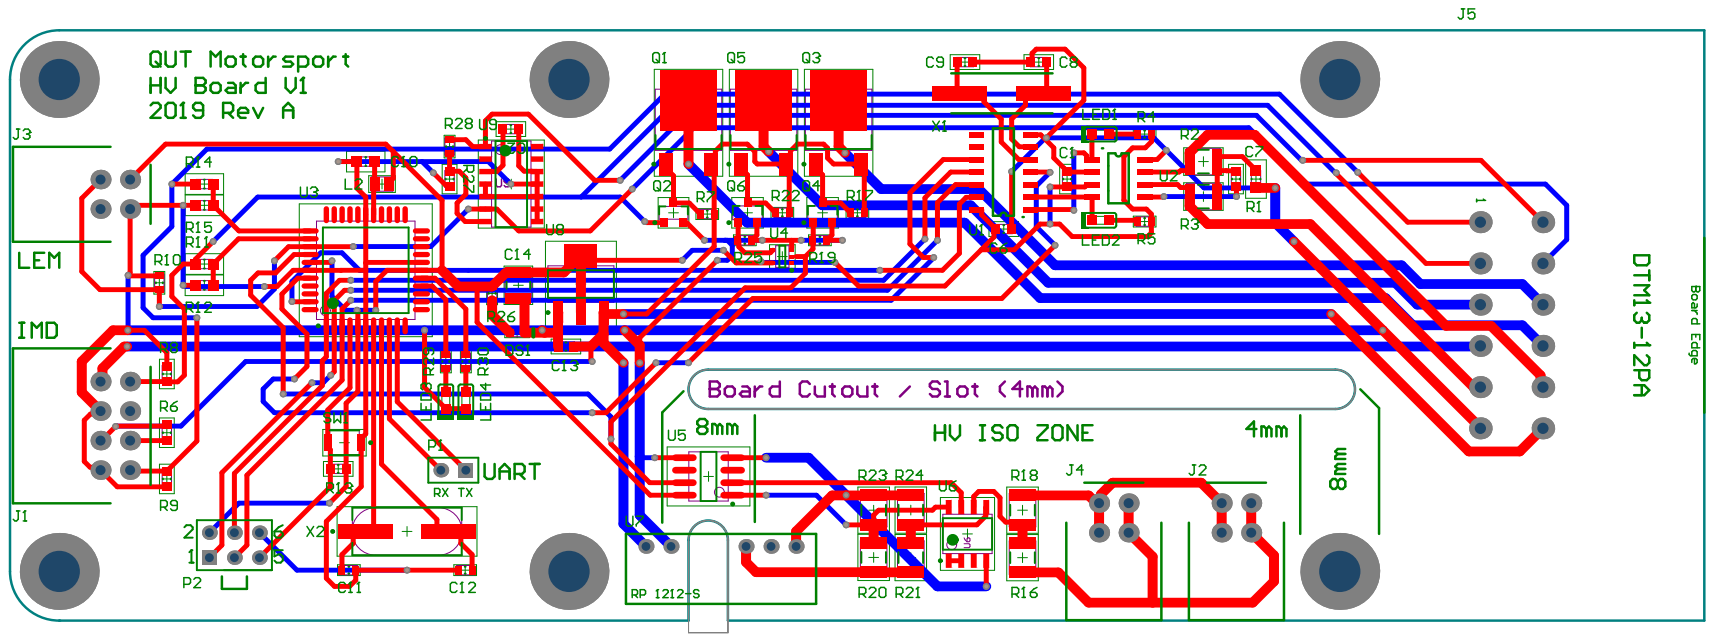
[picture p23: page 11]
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

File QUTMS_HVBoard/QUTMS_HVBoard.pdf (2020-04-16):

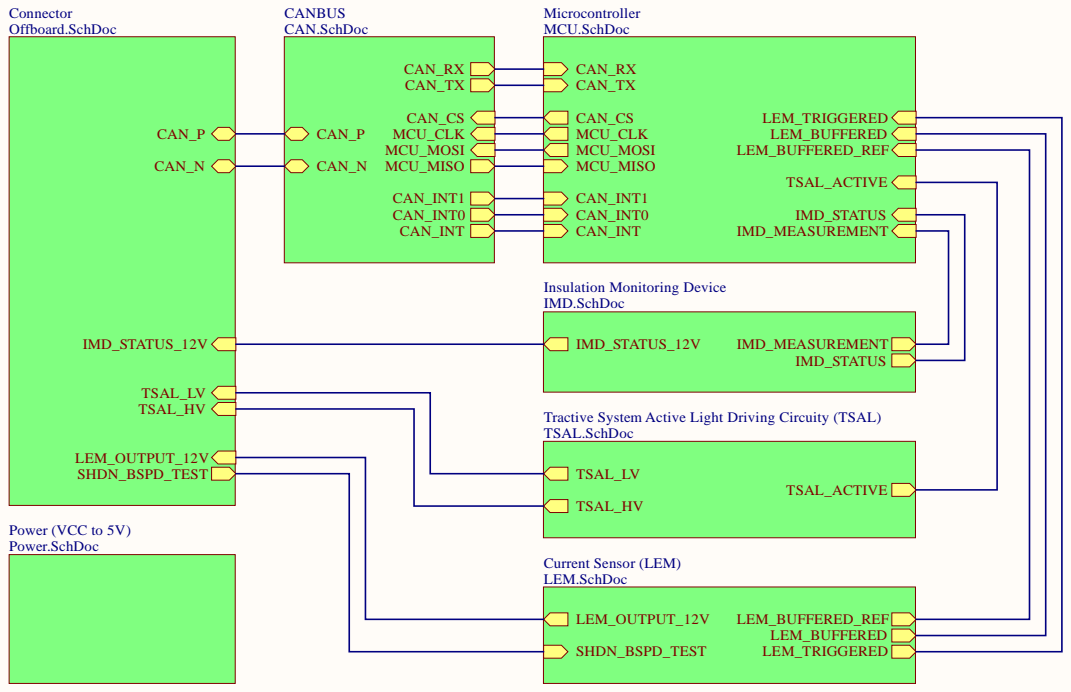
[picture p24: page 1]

Tractive System Active Light Driving Circuity (TSAL)
TSAL.SchDoc

QUTMS HVBoard V1.1 - Master Title
A4 Size: | Number: 1 | Revision: * | QUT Motorsport, O-120 O Block, QUT Gardens Point Brisbane, QLD, Australia

Date: 8/04/2020 Time: 12:07:02 PM | Sheet of


Preparing IMD Status signal for harness traversal

IMD Signal Buffers & 12V to 5V Shifters

Bender IMD Board Information
Part Number:
Serial Number:
Mat. Number:
Software Version:

https://www.bender.de/fileadmin/content/Products/d/e/IR155-32xx-V004_D00115_D_XXEN.pdf

QUTMS - HVBoard V1.1 - IMD Title

A4 Size: | Number: | Revision: | QUT Motorsport, O-120


Current Generation Resistor Selection (5kW Sim)

20 2.5A 50 1A | 4.8Ω 30 12Ω 12 | 5.76Ω 36 14.4Ω 14.4 | AWG 25 AWG 29

Shutdown Button Input Protection

Op Amp Compartor Guide
If VIN (+) > VREF (-) ? 5V : 0V
If VIN (+) < VREF (-) ? 0V : 5V

QUTMS - HVBoard V1.1 - LEM Title

https://www.lem.com/en/hass-200s
https://www.lem.com/en/hass-400s
https://www.lem.com/sites/default/files/products_datasheets/hass_50_600-s.pdf

A4 Size: | Number: | Revision: | QUT Motorsport, O-120


TSAL Signal Buffering and Inverting

If HV is on (+60V), then
ISO_ACTIVE line is
high

Still waiting for the new members
group who is designing the TSAL

Tractive System Active Comparator

Op Amp Compartor Guide
If VIN (+) > VREF (-) ? 5V
If VIN (+) < VREF (-) ? 0V

Isolated High Voltage Power Suply

Tractive System Spare Comparitor

QUTMS - HVBoard V1.1- TSAL Title

A4 Size: | Number: | Revision: | QUT Motorsport, O-120


MCU_PD2 | PD2 (PCINT/RXD1/26/INT0) 11

PD3 (PCINT/TXD1/27/INT1) 12

GND 18

GND 39

QUTMS HVBoard V1.1 - MCU Title
A4 Size: | Number: 5 | Revision: * | QUT Motorsport, O-120


CAN_RX | TP21 | RXD 4

STBY 8

Place TVS Diode between CANBUS
connection and 60R4 Termination
resistors

Signal data LED indicators
Grounds into TX RX lines

https://www.digikey.com.au/product-detail/en/microchip-technology/MCP2518FDT-H-SL/MCP2518FDT-H-SLCT-ND/10231406
https://www.digikey.com.au/product-detail/en/microchip-technology/MCP2517FDT-H-SL/MCP2517FDT-H-SLCT-ND/7801975

Check at time of order if these parts exist on LCSC

https://lcsc.com/product-detail/CAN-ICs_Microchip-Tech_MCP2561T-E-SN_Microchip-Tech-MCP2561T-E-SN_C87081.html

QUTMS - HVBoard V1.1 - CANBUS Title
A4 Size: | Number: 6 | Revision: * | QUT Motorsport, O-120

https://lcsc.com/product-detail/TVS_ON-Semicon_NUP2105LT1G_ON-Semicon-ON-NUP2105LT1G_C14486.htmlText


ors-MLCC-SMD-SMT

Q UTMS - HV Bo ard V1.1 - Power T i t l e

Size: A4 | N umber: 7 | Rev i s i o n : 2 | Q UT Mo t o r sp o r t, O-1 2 0 O B l ock, Q UT G a rden s P o i n t B r i s b a ne, QLD, A u s t r a l i a

/ / T ime: : : 3 PM | Sheet o f


TE DTM12 PCB Right Angle

QUTMS HVBoard V1.1 - Offboard Title | QUT Motorsport O-120 O Block QUT Gardens Point Brisbane, 4000

A4 Size: | 8 Number: | * Revision:

R:\Users\Jonn\Documents\git\qutms\QUTMS_HVBoard\hardware\QUTMS_HVBoard_V1_1\Offboard.SchDoc

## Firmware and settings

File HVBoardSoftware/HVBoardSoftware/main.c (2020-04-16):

/*
 * HVBoardSoftware.c
 *
 * Created: 3/08/2019 11:53:54 AM
 * Author : Jonn
 */ 

#define F_CPU 16000000

#include <avr/io.h>
#include <util/delay.h>
#include "main.h"

int init(void) {
	// Set Up Ports
	//		 LED B			  LED A
	PORTD = (1 << PORTD7) || (1 << PORTD6);
	return 0;
}

int main(void)
{
    while (1) 
    {
		LED_A_ON;
		LED_B_OFF;
		_delay_ms(500);
		LED_A_OFF;
		LED_B_ON;
		_delay_ms(500);
    }
}

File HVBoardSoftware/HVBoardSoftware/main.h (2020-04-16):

/*
 * main.h
 *
 * Created: 7/09/2019 8:40:00 PM
 * Author : Jonn
 */ 

// Define LEDs
// LED A => PIN 15, PD6
// LED B => PIN 16, PD7
#define LED_A_ON		PORTD |= 0b01000000
#define LED_A_OFF		PORTD &= ~0b01000000
#define LED_A_TOGGLE	PORTD ^= ~0b01000000

#define LED_B_ON		PORTD |= 0b10000000
#define LED_B_OFF		PORTD &= ~0b10000000
#define LED_B_TOGGLE	PORTD ^= ~0b10000000

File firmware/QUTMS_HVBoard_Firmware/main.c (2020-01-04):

/**
 * @file main.c
 * @author Zoe Goodward
 * @brief main.c
 * */

#define F_CPU 16000000UL /* CPU clock in Hertz */

#include <avr/io.h>
#include <util/delay.h>
#include <avr/interrupt.h>
#include <avr/pgmspace.h>

#include "input.h"
#include "UART.h"
#include "spi.h"
#include "adc.h"
#include "MCP2517.h"
#include "MCP2517_reg.h"

#define BIT_VALUE(reg, pin) ((reg>>pin) & 1)

uint8_t HV_BOARD_DATA[3] = {0};

/**
 * Consolidates all the functions required for the initialisation of
 * the HV board
 * @return void
 * */
void HV_board_init() 
{
	DDRD = 0b11000010; // LEDs as outputs
	DDRB = 0b10111000; // MOSI and SCK and CAN_CS as output, SS output
	// Set IMD Status pin as input - High = no fault, Low = failure
	DDRA = 0b00000000;
	
	CAN_CS_PORT |= (1 << CAN_CS); // CS high to turn off
	
	adc_init();
	uart0_init(9600);
	spi_init(0,0); // 1,0
	MCP2517_init();
	sei(); // Enable interrupts
}

int main(void)
{
    HV_board_init();
	
	uint8_t data[8] = {0};
	CAN_RECEIVE_ADDRESS receiveID;
	uint8_t numDataBytes;

	/**
	* @brief transmit message packet
	* CAN Packet 1
	* Byte 0									| Byte 1						| Byte 2						|
	* 0b  	  0,     	 0, 0, 0, 0,       000	| 0b00000000					| 0b00000000					|
	* HV Sense, IMD Alarm, -, -, -, IMD State	| LEM Measurement (bits 15-8)	| LEM Measurement (bits 7-0) 	|
	**/
	
    while(1) 
    {
		MCP2517_recieveMessage(&receiveID, &numDataBytes, data);
		if(receiveID == CAN_RECEIVE_ID_HV >> 18) {
			//LED_A_ON;		
			MCP2517_transmitMessage(CAN_SEND_ID_HV, 3, HV_BOARD_DATA); // Respond to CC Heartbeat
			//LED_A_OFF;
		}
		receiveID = 0;
		numDataBytes = 0;
		
		// Check whether the IMD Status pin is high or low (only after it's been plugged in/ running for min of 2s)
		if(BIT_VALUE(IMD_REG, IMD_STATUS) != 0) {
			data[0] |= 0b01000000;
			LED_B_ON;
		} else {
			data[0] &=~ 0b01000000;
			LED_B_OFF;
		}
		
		// Check the HV_SENSE_ON pin, High - TSAL is off, Low - TSAL is on
		if(BIT_VALUE(HV_SENSE_REG, HV_SENSE_STATUS) == 0) {
			data[0] |= 0b10000000; // Send 1 when TSAL on
			LED_A_ON;
		} else {
			data[0] &=~ 0b10000000;
			LED_A_OFF;
		}
		
		// Get the current LEM measurement
		uint16_t lemMeasurement = adc_read(0x01);
		HV_BOARD_DATA[1] = lemMeasurement >> 8;
		HV_BOARD_DATA[2] = lemMeasurement;
		//LED_A_TOGGLE;
		_delay_ms(100);
    }
}

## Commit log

2019-04-23 Migrated work from ShutdownV2 Repository
    [CAN.SchDoc, PCB1.PcbDoc, QUTMS_HVBoard.PrjPcb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]
2019-05-13 Added in LEM current sensor circuitry, started MCU, finished IMD connection and microfit library. Still need to fix CAN to latest version
    [CAN.SchDoc, IMD.SchDoc, LEM.SchDoc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]
2019-05-15 Finalised Rev 1 of HV board
    [Board.PcbDoc, CAN.SchDoc, IMD.SchDoc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]
2019-05-17 Finished HV Board V2 Rev 1, may need to change mircofit indentation in the future for compactness
    [Board.DWG, Board.PcbDoc, CAN.SchDoc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]
2019-06-10 Fixed up some small things, still have to fully spec header
    [CAN.SchDoc, LEM.SchDoc, Power.SchDoc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]
2019-06-12 Added small improvments, buffered LEM signal and filled in connectors
    [Board.PcbDoc, CAN.SchDoc, LEM.SchDoc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]
2019-06-14 Board finished, exported gerbers. Freeze Rev1
    [Board.PcbDoc, CAN.SchDoc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]
2019-06-15 Something changed
    [Board.PcbDoc, QUTMS_HVBoard.PrjPcb]
2019-09-18 Move pcb design docs into hardware folder
    [Board.DWG, Board.PcbDoc, CAN.SchDoc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]
2019-12-03 Fix numBytes being sent
    [main.c]
2020-01-12 Add comments about connector functions
    [Offboard.SchDoc]
2020-01-12 added a bunch more comments and fixed a few
    [CAN.SchDoc, IMD.SchDoc, LEM.SchDoc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]
2020-01-15 Changed programming header to right angle
    [Board.PcbDoc]
2020-01-15 Moved reset button to be accessible when the IMD is mounted above
    [Board.PcbDoc]
2020-01-15 Added a ground pin to the UART header
    [Board.PcbDoc]
2020-01-15 Moved CANBUS TX and RX leds to the edge of the board
    [Board.PcbDoc]
2020-01-15 Moved the oscillator crystal closer to the microcontroller
    [Board.PcbDoc]
2020-01-15 Tidied up traces
    [Board.PcbDoc]
2020-01-15 Tidied up traces even more
    [Board.PcbDoc]
2020-01-27 Changed the headers to match those on the board
    [MCU.SchDoc]
2020-01-27 Create schematic symbol and footprint for opto-isolator
    [QUTMS_OptoIsolator.PcbLib, QUTMS_OptoIsolator.SchLib]
2020-01-27 Replaced previous TSAL detection circuit with new
    [Board.PcbDoc, QUTMS_HVBoard.PrjPcb, TSAL.SchDoc]
2020-01-31 Removed DC-DC converter, transistor and pull down resistor, switched HV sense on/off
    [Board.PcbDoc, TSAL.SchDoc]
2020-01-31 Aligned IMD mounting holes correctly
    [Board.PcbDoc]
2020-02-01 change resistor power capacity and re-route a little
    [Board.PcbDoc, TSAL.SchDoc]
2020-02-01 fix CAN netlist names
    [Board.PcbDoc, CAN.SchDoc, Offboard.SchDoc]
2020-02-01 fix some missing traces
    [Board.PcbDoc]
2020-02-01 change header to right angle
    [Board.PcbDoc, MCU.SchDoc]
2020-02-01 remove stray trace
    [Board.PcbDoc]
2020-02-01 remove now un-used cutout
    [Board.PcbDoc]
2020-02-01 add net labels to UART lines
    [Board.PcbDoc, MCU.SchDoc]
2020-02-01 add hv symbol to hv iso zone
    [Board.PcbDoc]
2020-02-01 make hyperlink open specific page
    [IMD.SchDoc]
2020-02-01 add hyperlink to ev rule
    [TSAL.SchDoc]
2020-02-01 oops that wont work just yet
    [TSAL.SchDoc]
2020-02-01 clean up old schematic
2020-02-01 Added HV Board System Diagram.drawio
2020-02-01 Update HV Board System Diagram.drawio
2020-04-16 Added the V1.1 of this board. Completely rebuilt
    [430450400.stp, 430450600.stp, 430450800.stp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]
